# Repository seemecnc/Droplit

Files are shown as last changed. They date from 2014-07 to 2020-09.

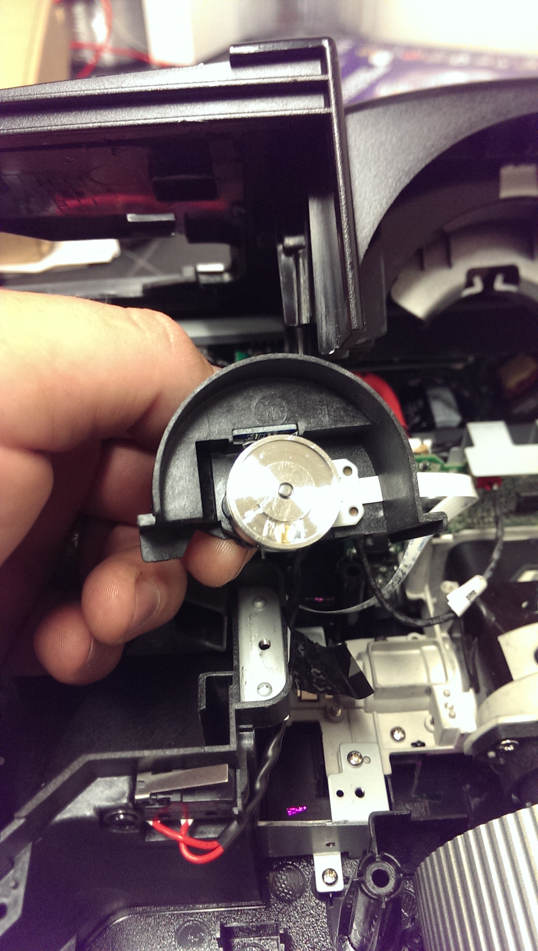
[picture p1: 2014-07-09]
DevPhotos/IMAG0862.jpg

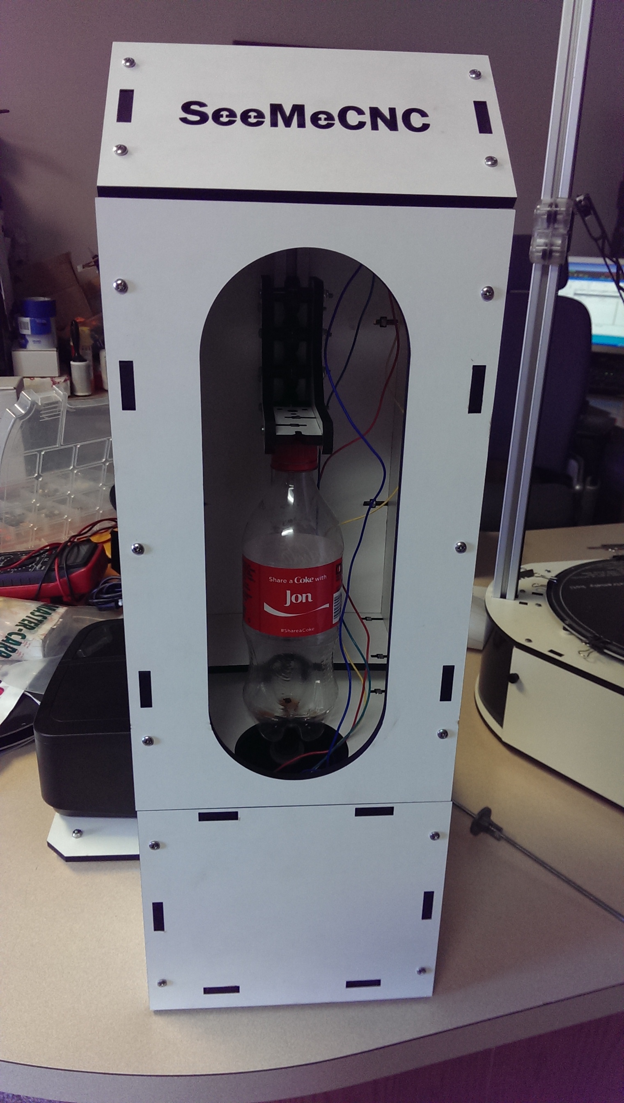
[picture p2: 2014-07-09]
DevPhotos/IMAG0863.jpg

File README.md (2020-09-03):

Droplit
=======

Droplit 3D Printer by SeeMeCNC

This project is released on good will by us.  All designs are originally drawn by us, however many of our ideas
may have obviously had influence from the RepRap community, hence the GPL license.  Feel free to use/modify these 
files for any reason, just share attribution if you do, thanks!

For the STL files, see http://repables.com/r/371/

Electronics/Firmware Used as of 7/14 are:

Arduino UNO r3 
http://arduino.cc

Grbl Shield by Synthetos
http://synthetos.com

Projector
TBD
Testing with IN Focus 116a and Acer P1283

Firmware is modified grbl 0.8c available from
http://github.com/grbl/grbl

# visit SeeMeCNC .com menu item SUPPORT for more docs & guides for RAMBo controlled SeeMeCNC 3D printers.

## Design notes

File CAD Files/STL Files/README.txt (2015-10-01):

38710 M5 Anti Backlash nut is used with M5x0.8 threaded rod and two TALL M5 nuts
One is sunk in the bottom of the part, then a spring (TBD) is put over the rod and
a second nut is then threaded on, and the spring takes out any backlash

You can just print Droplit_Plate.STL for all the required parts.

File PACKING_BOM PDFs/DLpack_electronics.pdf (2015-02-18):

# Packing List

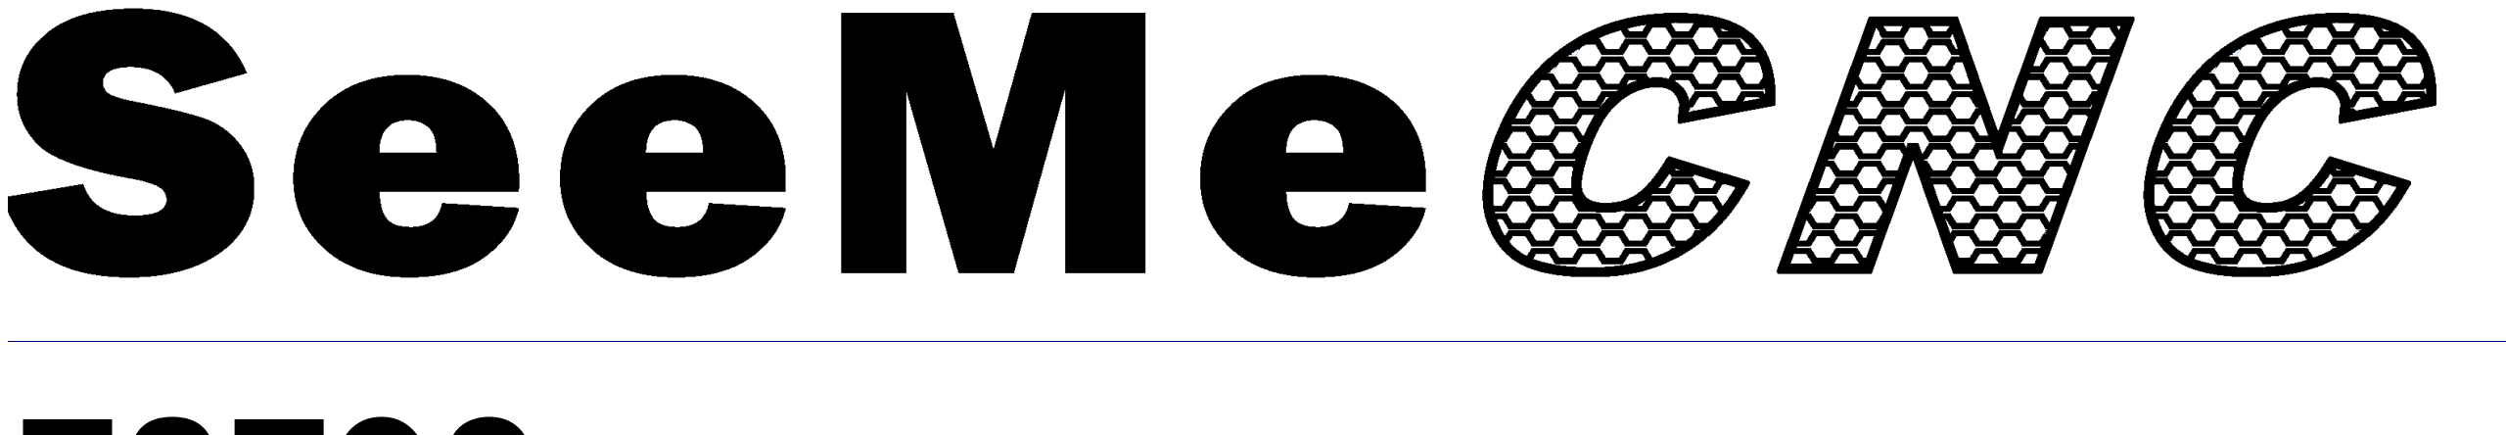
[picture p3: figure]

# 78793 DropLit Electronics Pack

item # | qty | Description | Where is this item used?
26801 | 1 | Arduino UNO R3 SMT | Electronics Bay
26802 | 1 | GShield 3 Axis Stepper Motor Board | Electronics Bay
26076 | 1 | SW143-ND SPDT Micro Switch | Top of TSLOT
26174 | 2 | Spade Terminal Crimp for Switch | Switch
26501 | 1 | Nema 17 Stepper Motor 4800gcm holding torque | Top of Machine
26175 | 1 | Rocker Switch, Black Round | Electronics Bay
26732 | 1 | ATX Power Supply 550 Watt Viotek | Electronics Bay
26164 | 8 | Wire Tie (small) | Frame
26728 | 3 | 26AWG 7 Strand Wire BLACK Thin Wall PVC | Electronics to End Stop (measured in feet)
26725 | 3 | 26AWG 7 Strand Wire WHITE Thin Wall PVC | Electronics to End Stop (measured in feet)
©2014 SeeMeCNC | 18-Feb-15 | 78793 | DropLit Electronics Pack | Page 1 of 1

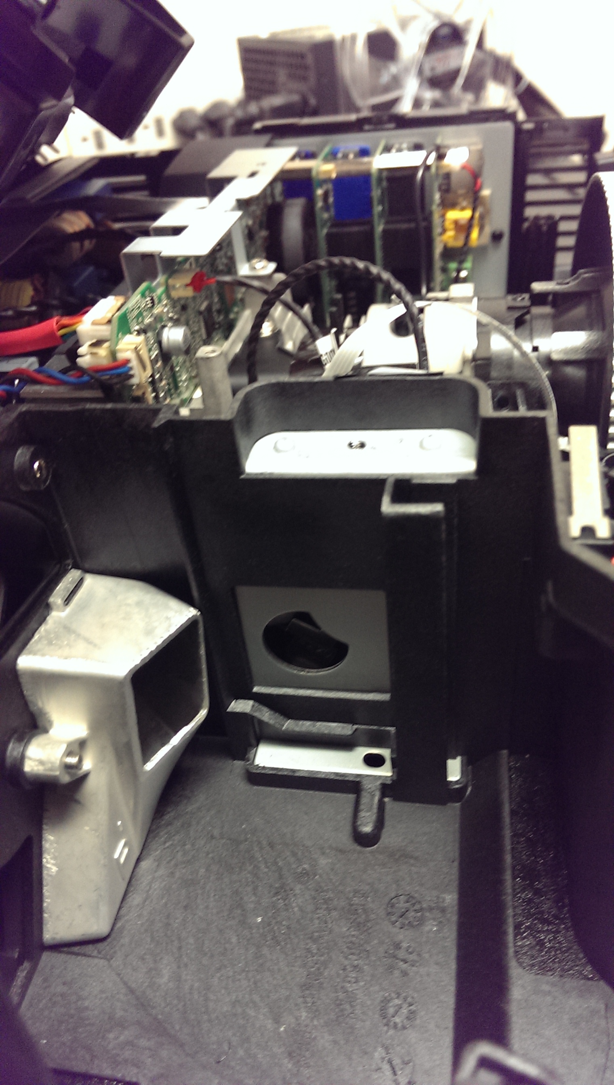
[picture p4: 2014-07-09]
DevPhotos/IMAG0861.jpg

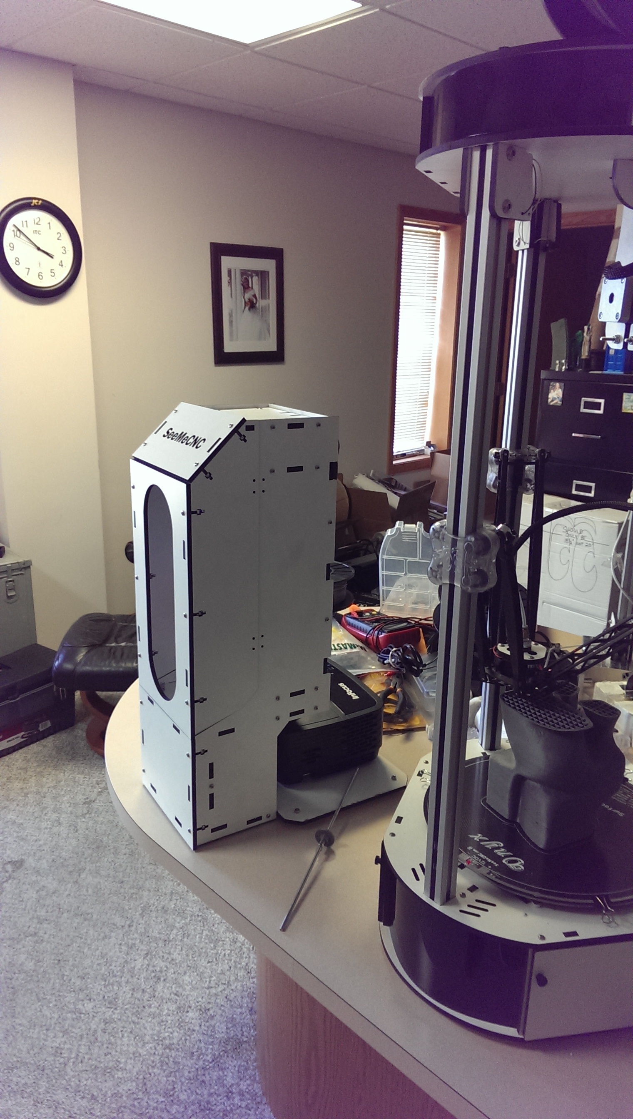
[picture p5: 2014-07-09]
DevPhotos/IMAG0865.jpg

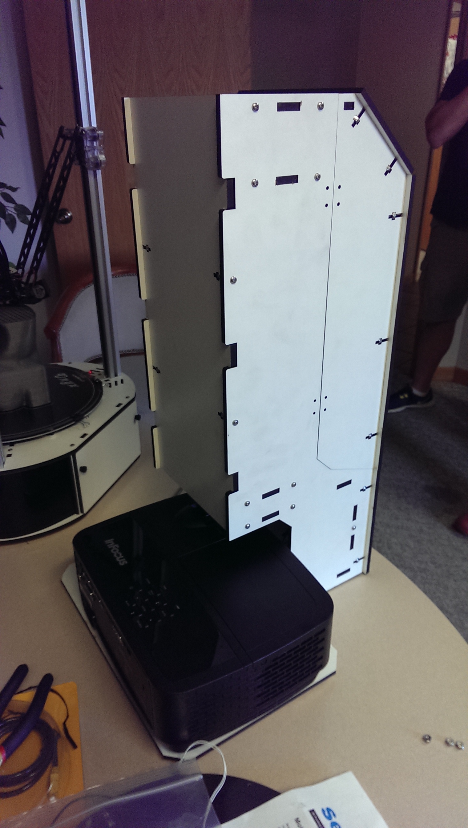
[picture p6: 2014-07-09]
DevPhotos/IMAG0864.jpg

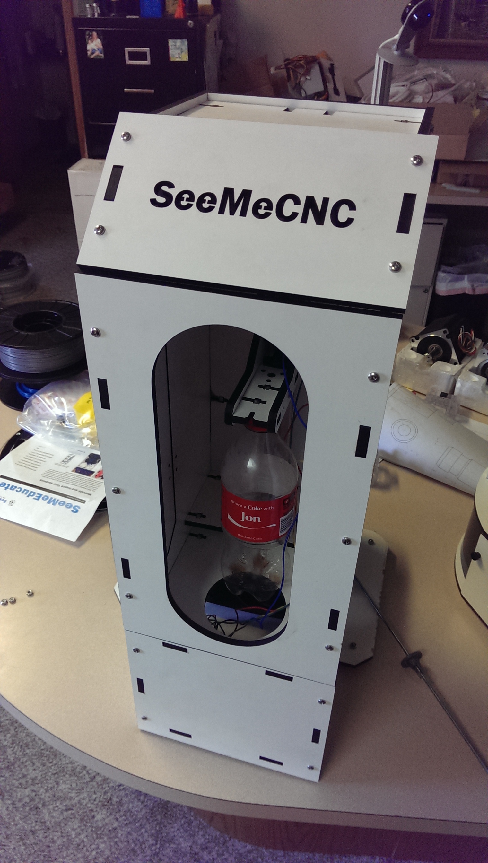
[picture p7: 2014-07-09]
DevPhotos/IMAG0866.jpg

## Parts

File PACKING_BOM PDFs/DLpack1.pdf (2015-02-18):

# Packing List

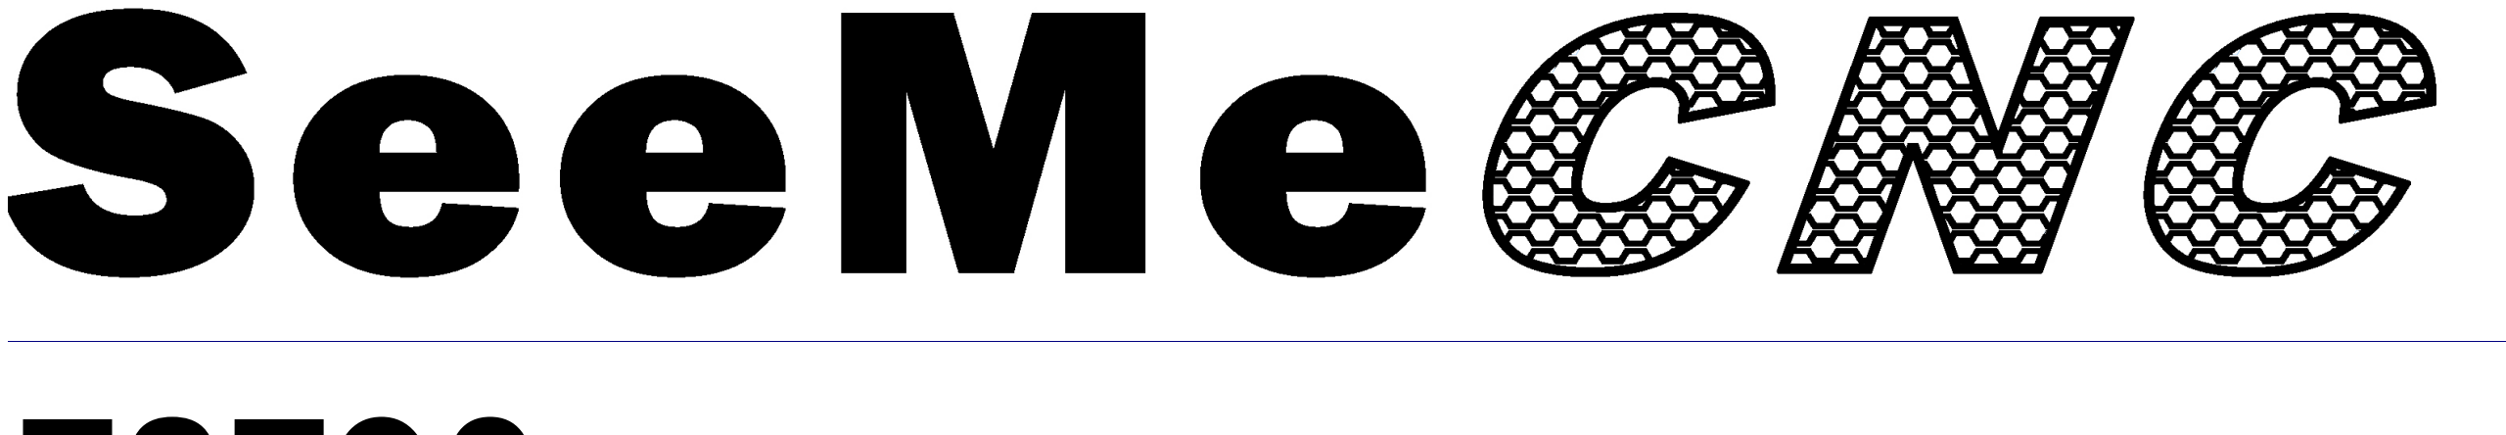
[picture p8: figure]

# 78790 DropLit Hardware Bag #1

item # | qty | Description | | Where is this item used?
30354 | 3 | M5 Zinc Plated Heavy Nut | Two used for anti backlash nut and one to secure z rod to coupler
35008 | 6 | 1/4ID x 5/8OD x .196W Ball Bearing R4ZZ | Cheapskate truck assembly
30033 | 57 | 6-32 x 1" L Phillip Pan Head Screw Stainless | Frame Assembly
30037 | 6 | 6-32 x 2.0" L Phillip Pan Head Screw 18-8 SS | Cheepskate Truck Assembly
30006 | 10 | SHCS 6-32 x 5/8" | 18-8 SS | Hinges and Door latch
30164 | 75 | 6-32 Nylon Lock Nut Stainless Steel | Entire Assembly
17505 | 4 | Leg for 44010 Foot | | Frame Base
44010 | 4 | Rubber Foot | | Frame Base
29998 | 4 | 10-32 x 5/8" Pan Head Screw Nylon | Frame Base
30170 | 4 | 10-32 Nylon Finish Nut | Frame Base
71505 | 4 | Plastic Bearing Roller 1/8"ID x 3/8"OD x 0.156"W | Electronics Mount
30121 | 4 | 6-32 x 1/2" Slotted Pan Head Screw Nylon | Power Supply
32005 | 6 | T SLOT Nut for 1" size 1/4-20 | TSLOT
30419 | 6 | 1/4-20 x 1/2" Button Head Cap Screw Stainless | TSLOT
30650 | 6 | 2-56 x 5/8"L Pan Head Phillips Machine Screw ( zinc plate ) | Attach Electronics
30642 | 6 | 2-56 Finish Nuts ( zine plate ) | Attach Electronics
30318 | 4 | M3 - .50 x1 0mm Phillip Pan Head Machine Screw 18-8 SS | Attach Stepper Motor
30449 | 4 | #4 SAE Flat Washer Stainless Steel | Attach Stepper Motor
30262 | 8 | #6 x 1/2"L Phillip Pan Head Sheet Metal Screw Type B Stainless | Vat Hold Down Assembly
31250 | 1 | .300 OD x .030 wire x 1/2L SS Compression spring | Antibacklash
30223 | 2 | 10-32 Blind T-Nut (Zinc Plate) | Vat Mount
30038 | 2 | M3-.5 x 6mm Set Screw Allen | Motor Coupler
30039 | 1 | 1.5mm Allen Key for M3-.5 set screws | Motor Coupler
30172 | 4 | 10-32 x 3/4" Knurled Thumb Screw Black Nylon | Mirror mount, vat hold down and platform
©2014 SeeMeCNC | 18-Feb-15 | 78790 | DropLit Hardware Bag #1 | Page 1 of 1

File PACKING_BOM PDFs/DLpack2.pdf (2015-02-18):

# Packing List

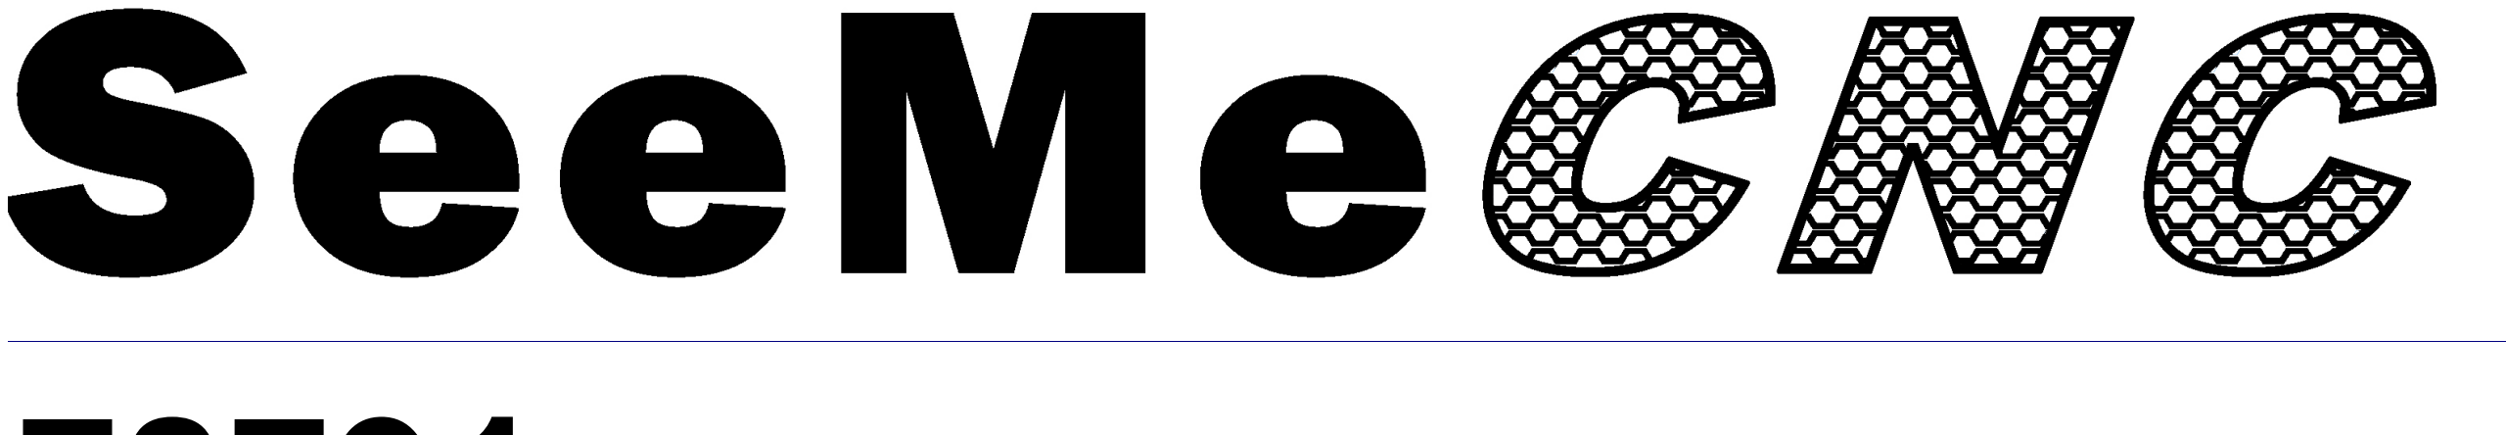
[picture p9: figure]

# 78791 DropLit Hardware Bag #2

item # | qty | Description | Where is this item used?
78704 | 6 | Eccentric Spacer | 0
38710 | 1 | M5 Anti Backlash Nut carrier | 0
78748 | 1 | Door Latch | 0
78755 | 2 | R4 Bearing Bushing Block | 0
78705 | 1 | M5 Threaded Rod 12" | Z Axis
38703 | 1 | 5mm Shaft Coupler | Z Axis
78702 | 1 | TSLOT - 15.25" | Z Axis
78749 | 1 | Build Plaform Standoff | Cheapskate Assembly
87941 | 12 | R4 Bearing Sleeve | Cheapskate Assembly
78740 | 2 | Hinge 1x1 | Door Hinges
78708 | 1 | Mirror 75mm x 75mm | Mirror
©2014 SeeMeCNC | 18-Feb-15 | 78791 | DropLit Hardware Bag #2 | Page 1 of 1

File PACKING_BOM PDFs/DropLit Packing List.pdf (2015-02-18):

# Packing List

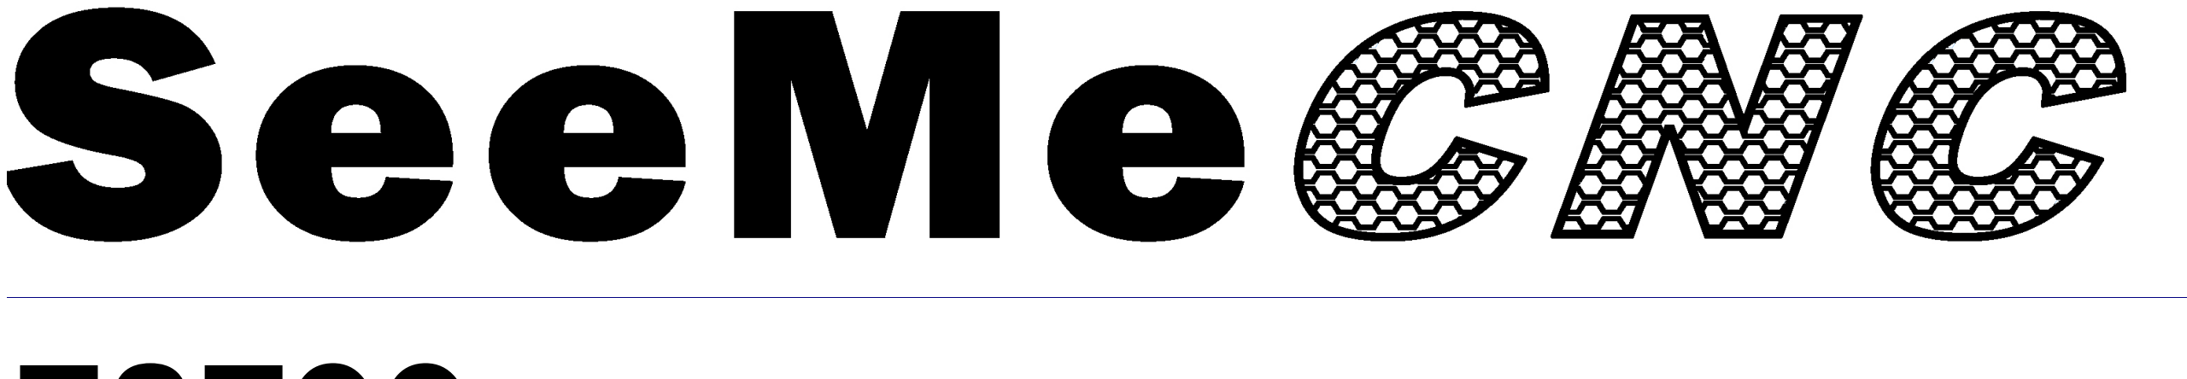
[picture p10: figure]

# 78799 DropLit DIY Kit

item # | qty | Description | Where is this item used?
78792 | 1 | DropLit Hardware Bag #3 | 0
78793 | 1 | DropLit Electronics Pack | 0
78791 | 1 | DropLit Hardware Bag #2 | 0
78790 | 1 | DropLit Hardware Bag #1 | 0
78794 | 1 | DropLit Lasercut Melamine Sheets (qty 4) | 0
78795 | 1 | DropLit Lasercut Acrylic Parts | 0
©2014 SeeMeCNC | 18-Feb-15 | 78799 | DropLit DIY Kit | Page 1 of 1

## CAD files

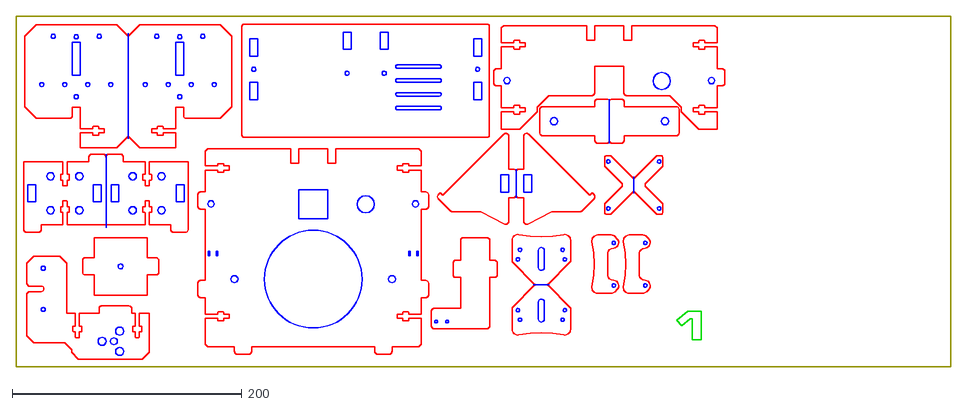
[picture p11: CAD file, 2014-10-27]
CAD Files/DXF LC Files/787xx Rev4/SHEET1.DXF
812.8 x 304.8

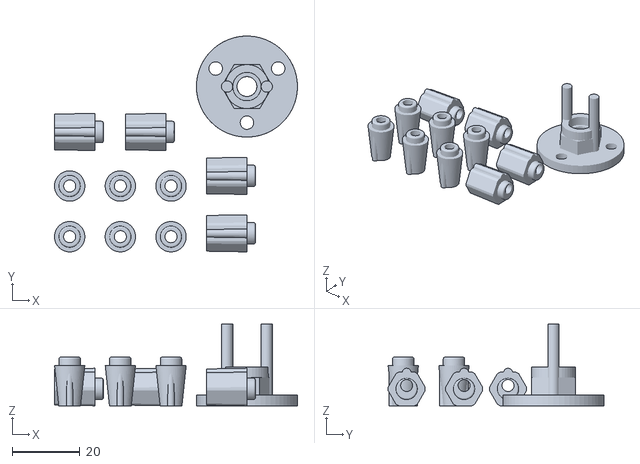
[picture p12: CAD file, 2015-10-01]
CAD Files/STL Files/Droplit_Plate.STL
71.9 x 63.9 x 24.1

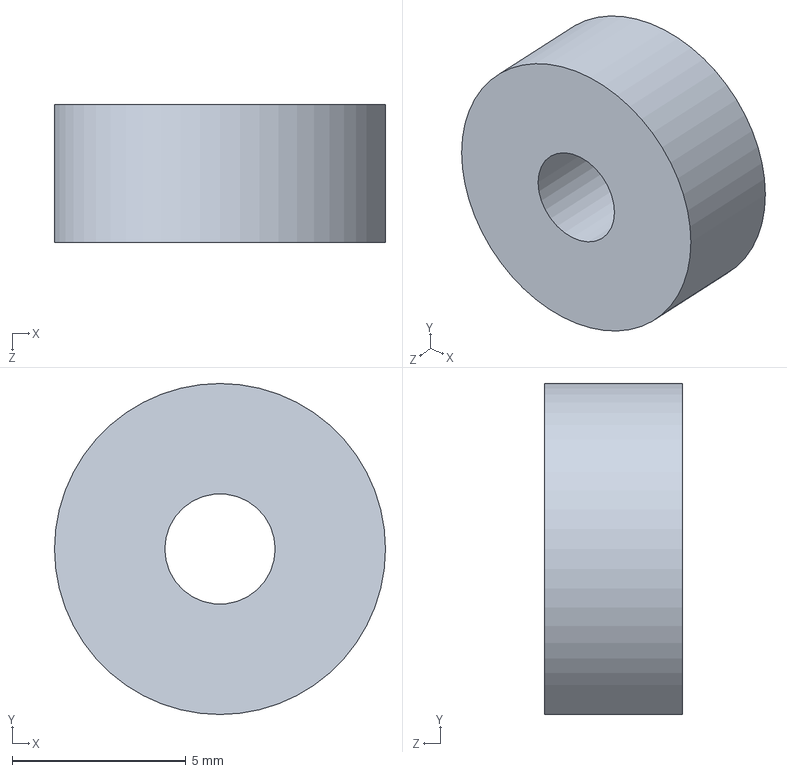
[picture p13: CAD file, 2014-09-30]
CAD Files/SW Files/plastic spacer.SLDPRT
9.53 x 9.53 x 3.96 mm

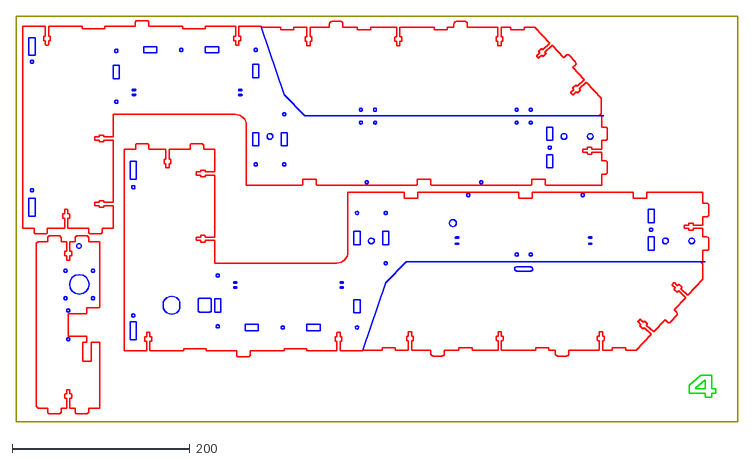
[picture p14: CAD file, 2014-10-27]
CAD Files/DXF LC Files/787xx Rev4/SHEET4.DXF
812.8 x 457.2

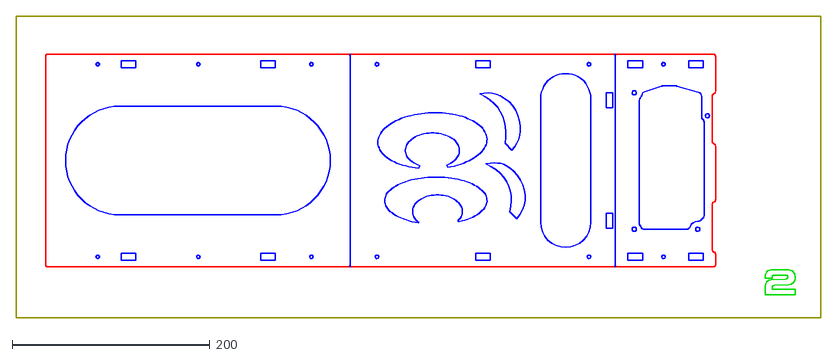
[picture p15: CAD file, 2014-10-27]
CAD Files/DXF LC Files/787xx Rev4/SHEET2.DXF
812.8 x 304.8

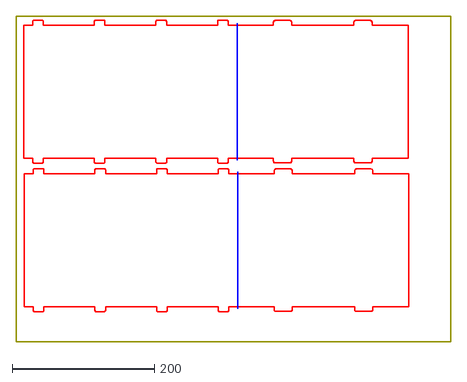
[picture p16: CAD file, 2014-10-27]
CAD Files/DXF LC Files/787xx Rev4/ACRYLICSHEET.DXF
609.6 x 457.2

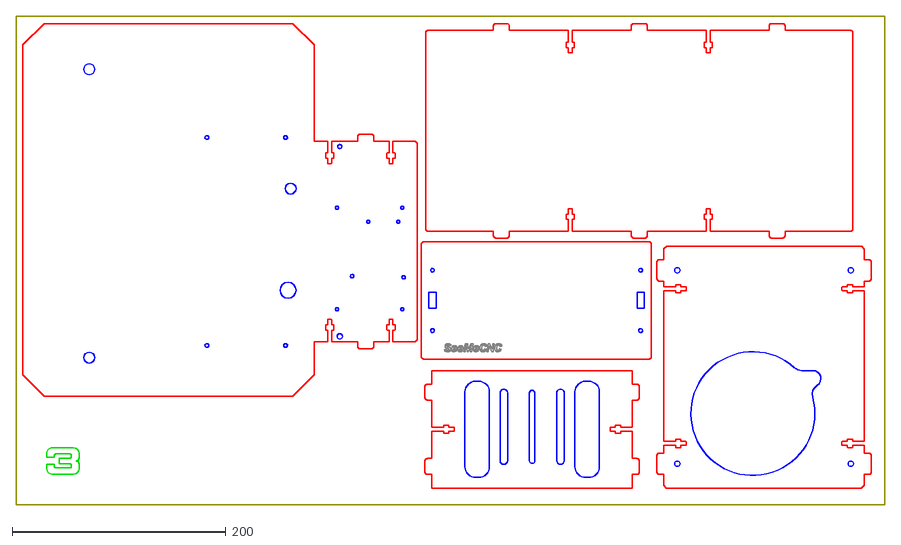
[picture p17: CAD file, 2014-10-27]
CAD Files/DXF LC Files/787xx Rev4/SHEET3.DXF
812.8 x 457.2

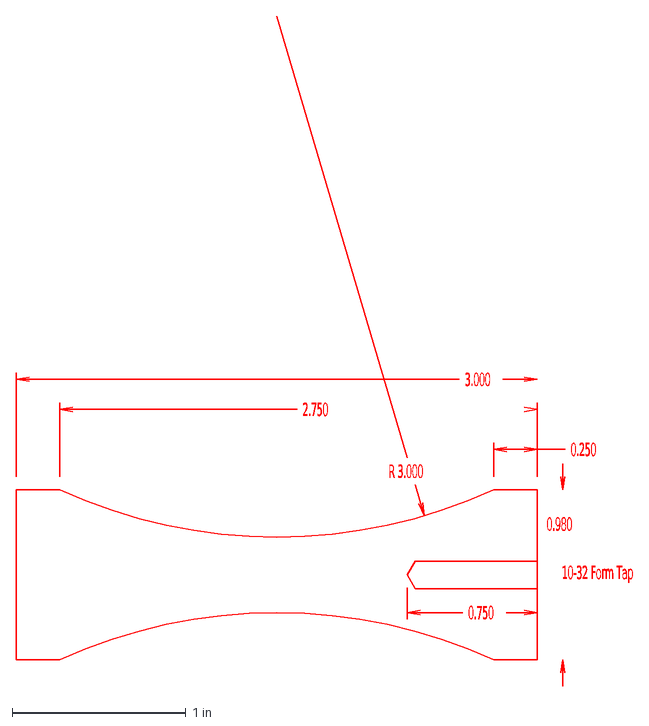
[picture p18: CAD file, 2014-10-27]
CAD Files/78749-PLATFORM-STANDOFF-ALUMINUM.DXF
10-32 Form Tap
0.980
0.250
3.000
0.750
2.750
R 3.000

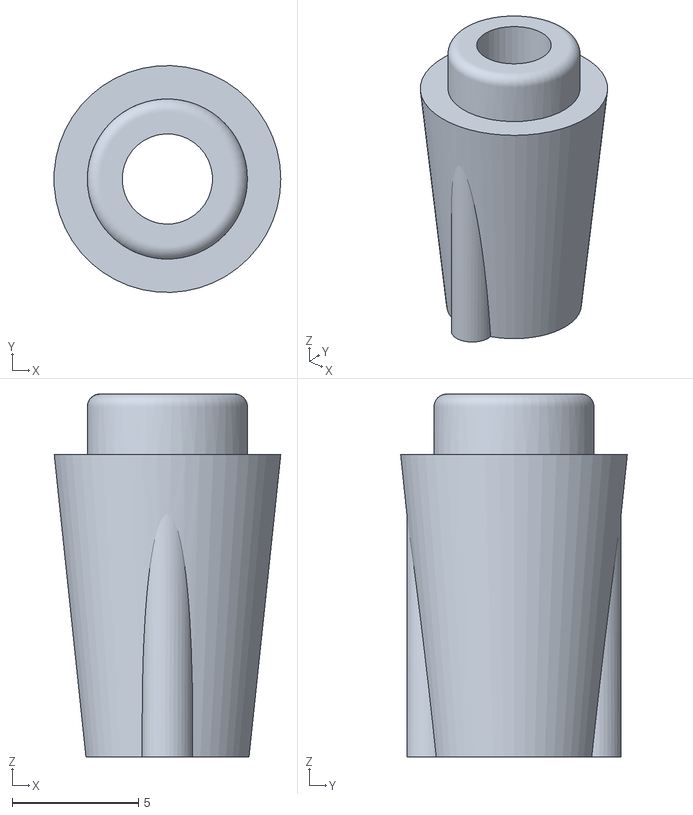
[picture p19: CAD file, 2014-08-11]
CAD Files/STL Files/78703 R4 Bearing Bushing.STL
8.99 x 9.00 x 14.4

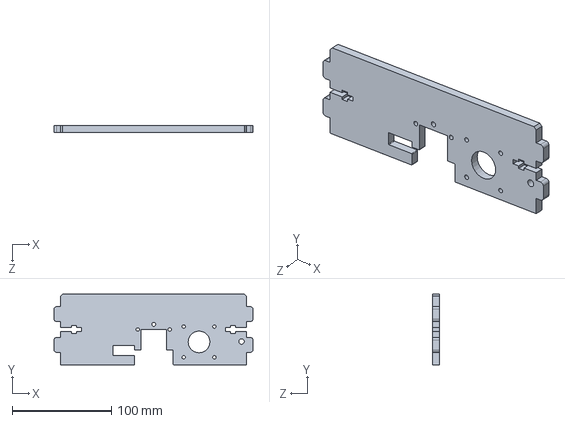
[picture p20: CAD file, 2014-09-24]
CAD Files/SW Files/78715 Motor Mount x1.SLDPRT
200.8 x 71.4 x 6.60 mm

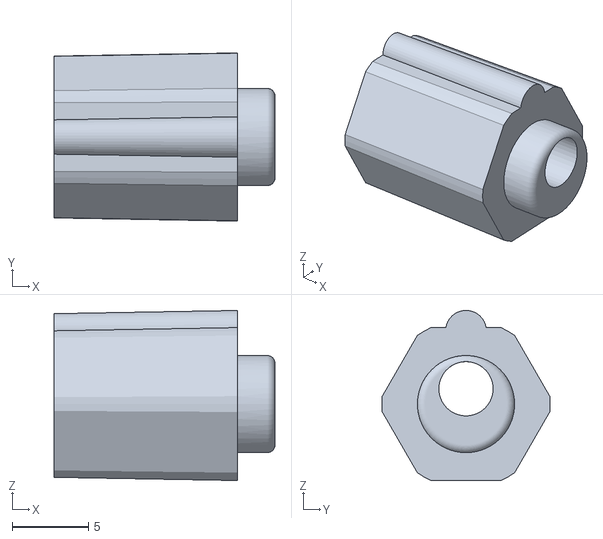
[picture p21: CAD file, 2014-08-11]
CAD Files/STL Files/78704 R4 Eccentric Bushing.STL
14.4 x 11.0 x 11.1

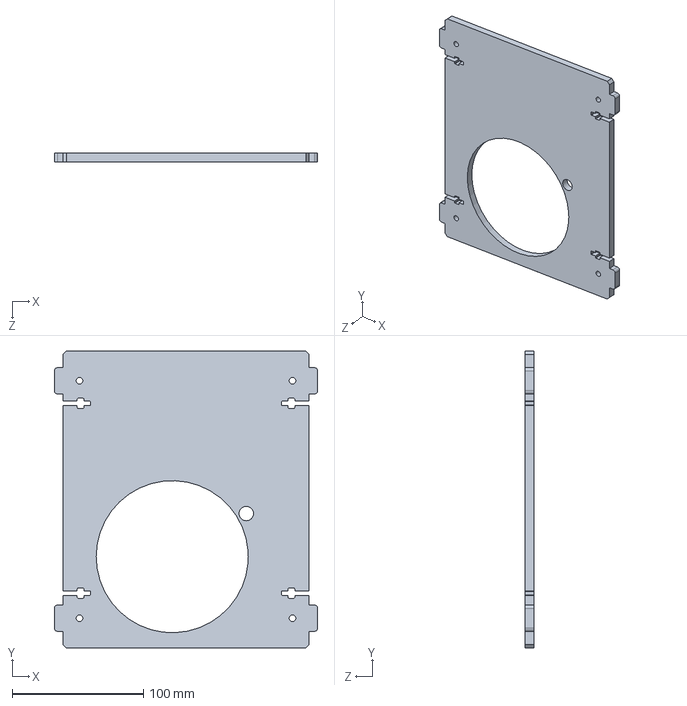
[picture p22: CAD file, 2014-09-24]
CAD Files/SW Files/78734 PSU Base Plate x1.SLDPRT
200.8 x 226.4 x 6.60 mm

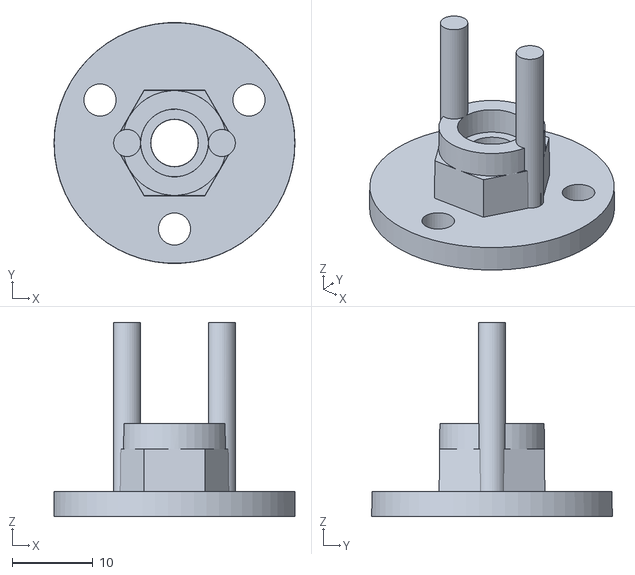
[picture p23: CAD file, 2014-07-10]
CAD Files/STL Files/38710 M5 Anti Backlash Nut Carrier.STL
29.9 x 29.9 x 24.1

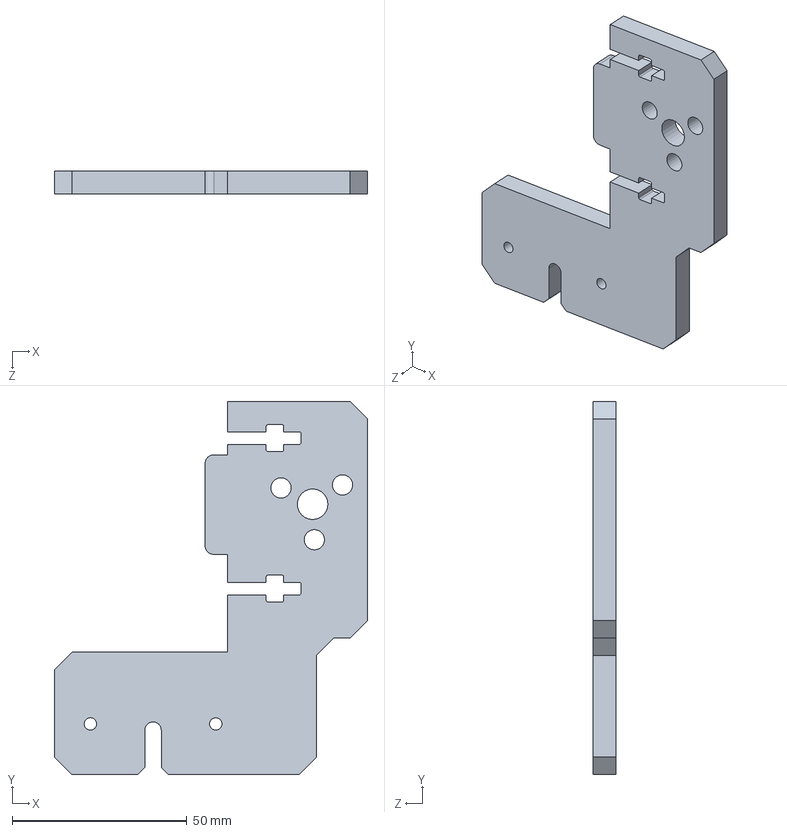
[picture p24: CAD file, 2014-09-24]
CAD Files/SW Files/78713 Carriage Mounting Plate for R4 x1.SLDPRT
89.6 x 106.7 x 6.60 mm

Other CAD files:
CAD Files/SW Files/78716 Top Plate x1.SLDPRT
CAD Files/DXF LC Files/787xx Rev4/78712 Base Side A x1.DXF
CAD Files/SW Files/78720 Back Cover x1.SLDPRT
CAD Files/DXF LC Files/787xx Rev4/78721 Cover Side A x1.DXF
CAD Files/DXF LC Files/787xx Rev1/ALLPARTS.DXF
CAD Files/DXF LC Files/787xx Rev2/78706 Window Panel x1 Acrylic.DXF
CAD Files/DXF LC Files/787xx Rev2/78710 DL Carriage Plate x2.DXF
CAD Files/DXF LC Files/787xx Rev2/78711 Base x1.DXF
CAD Files/DXF LC Files/787xx Rev2/78712 Base Side x2.DXF
CAD Files/DXF LC Files/787xx Rev2/78713 Carriage Mounting Plate for R4 x1.DXF
CAD Files/DXF LC Files/787xx Rev2/78714 Logo Panel x1 Acrylic.DXF
CAD Files/DXF LC Files/787xx Rev2/78715 Motor Mount x1.DXF
CAD Files/DXF LC Files/787xx Rev2/78716 Top Plate x1.DXF
CAD Files/DXF LC Files/787xx Rev2/78717 TSLOT Mount x2.DXF
CAD Files/DXF LC Files/787xx Rev2/78718 Dish Base x1..DXF
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

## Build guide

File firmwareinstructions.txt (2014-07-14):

Links for installing GRBL on an Arduino UNO

Download the hex file from this git repo
https://github.com/grbl/grbl-builds/blob/master/builds/grbl_v0_8c_atmega328p_16mhz_9600_build20131207.hex

Download XLoader from this link.  You will use it to upload the pre-compiled hex file downloaded above (the firmware)
http://russemotto.com/xloader

GRBL Wiki on GitHub describing how to compile it from source if you're super nerdy 
https://github.com/grbl/grbl/wiki/Compiling-Grbl

Instructions on using Grbl and how to modify it
https://github.com/grbl/grbl/wiki

To compile form source on windows download WinAVR
Install it in the DEFAULT DIRECTORY!!! which is usually C:...  DON'T CHANGE IT
in the default grbl folder, open a command prompt and run make clean then run make grbl.hex 
and you should be all good to go!

There is a file in the Firmware directory named configure.gcode that you can run to set the 
grbl defaults if you do not want to compile/etc... your own.  You can send that with any software to
the machine, or copy/past line be line the settings to configure the machine

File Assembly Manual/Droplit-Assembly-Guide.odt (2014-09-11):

Welcome to the Assembly Guide for the DropLit 3D printer.

Version 0.02, September 10th, 2014

Copyright 2014 by Gene Buckle

Licensed as Creative Commons Attribution-ShareAlike 3.0

Questions or corrections should be emailed to geneb@deltasoft.com

Disclaimer text provided by LulzBot

# READ ME FIRST!

READ THIS MANUAL COMPLETELY BEFORE ASSEMBLING AND POWERING UP

YOUR PRINTER!

###### Hazards and Warnings

###### The SeeMeCNC DropLit 3D printer has motorized parts. When the printer is in operation always be aware of possible hazards.

###### Electric Shock Hazard

###### Never open the electronics bay of the printer while the printer is powered on. Before removing

###### the access door, always power down the printer and unplug the AC line cord.

###### Fire Hazard

###### Never place flammable materials or liquids on or near the printer when powered on or in

###### operation.

###### Pinch Hazard

###### When the printer is in operation, take care to never put your fingers in the moving parts,

###### including the belts, pulleys or gears. Also, tie back long hair or clothing that can get caught in

###### the moving parts of the printer.

###### Static Charge

###### Make sure to ground yourself before touching the printer, especially the electronics.

###### Electrostatic charges can damage electronic components. To ground yourself, touch a

###### grounded source.

###### Age Warning

###### For users under the age of 18, adult supervision is recommended. Beware of choking hazards

###### around small children.

# 0 – Introduction and Acknowledgments

I’d like to welcome you to the DropLit assembly guide!

Please read this entire guide before you begin assembly of your new DropLit! It will help you avoid any unpleasant surprises and will ensure that you’ve got everything you need BEFORE you need it! Understand that the photographs in this assembly guide do NOT tell the whole story of each step! Make sure you read and understand the accompanying text for each step!

A quick note on the Arduino Uno and the “grbl” Shield. These two devices work in combination to control the DropLit and are very static sensitive, so please don't take them out of the bags they ship in until you're ready to install them.

# 1 – Required and Optional Tools And Materials

Before you begin assembly of your Rostock MAX v2, please make sure you’ve got everything on the following list of tools and additional materials.

- P1 & P2 sized Phillips screwdrivers
- Standard flat head screwdriver
- Wire strippers
- Wire cutters
- Battery powered screwdriver. If you ever needed an excuse to buy one of these, THIS IS IT.
- Blue thread locking compound (Loctite or Permatex Threadlocker Blue)
- Waxed lacing cord. You can use this in place of wire ties in pretty much any application. You can find it here: http://www.skygeek.com/wht-string.html. While expensive, you'll never really need to buy a wire tie again and it'll likely last you the rest of your life. :)

# 2 – Visual Bill of Materials

Your DropLit kit should contain a wrapped pack of Melamine parts, three bags of parts (two bags of hardware, one bag of electronic parts) a short section of aluminum extrusion and a power supply.

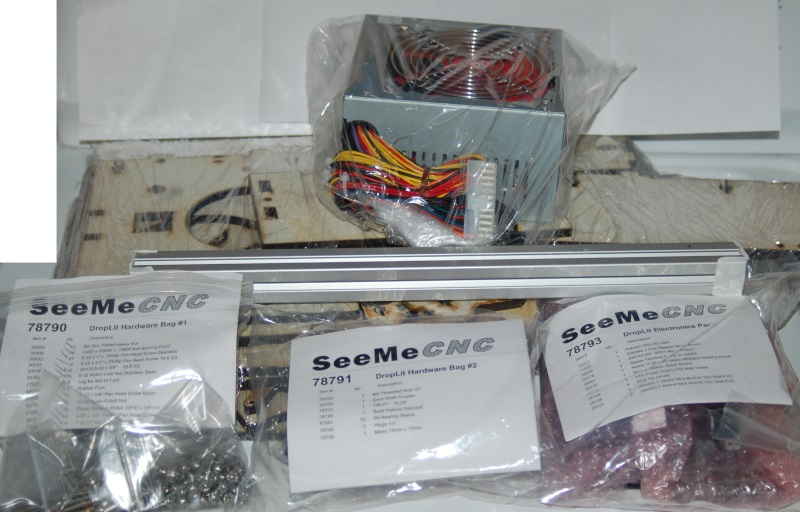
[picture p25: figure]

Fig. 2-1: DropLit package contents.

The Melamine parts are covered with a special cutting mask that prevents the laser cutting operation from depositing cutting residue on the Melamine surface. You'll need to remove all of this material before beginning construction. This process is called the Five Stages of Masking Tape.

1. Denial - Oh there's no way I need to scrape all this tape off those parts? Do I?

2. Anger - @#$%@#! This sucks! I've NEVER SEEN SO MUCH TAPE IN ONE PLACE IN MY LIFE!

3. Bargaining - “Well hi there, Significant Other! Would you PLEASE remove all this tape for me? PLEASE?”

4. Depression - This tape hates me. *sobs quietly*

5. Acceptance - Well I suppose if I'm ever going to get this thing built, I'd better get on with it and get all this tape removed...*sigh*

Ok, it's not THAT bad, it just seems like it. It beats having sticky ash product all over your nice and clean Melamine parts. :)

For those that aren't sure how to identify the various screw types, Bolt Depot has made available some excellent references. I would recommend Fastener Basics (http://www.boltdepot.com/fastener-information/Printable-Tools/Fastener-Basics.pdf) and their Fastener Type Chart (http://www.boltdepot.com/fastener-information/Type-Chart.aspx).

DropLit Hardware Bag #1

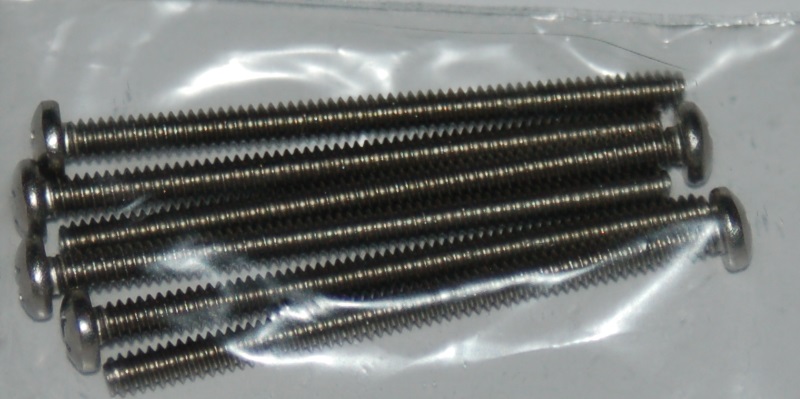
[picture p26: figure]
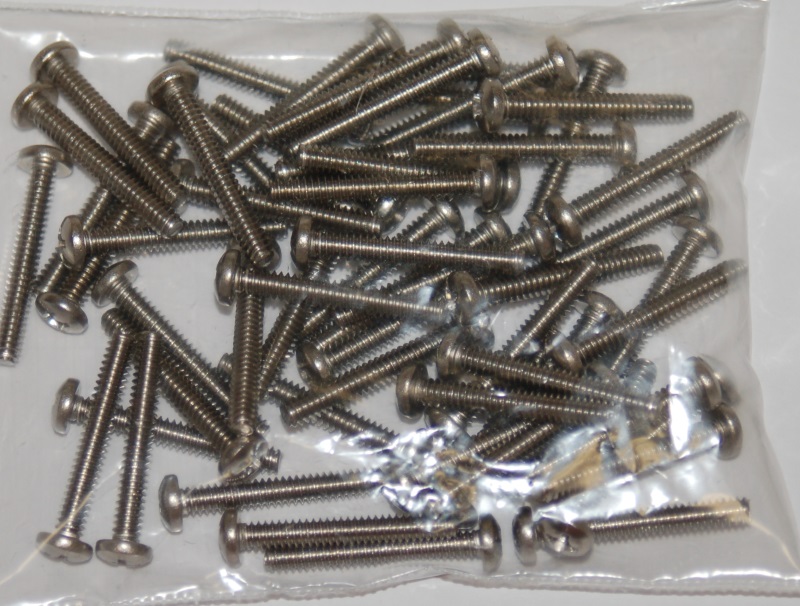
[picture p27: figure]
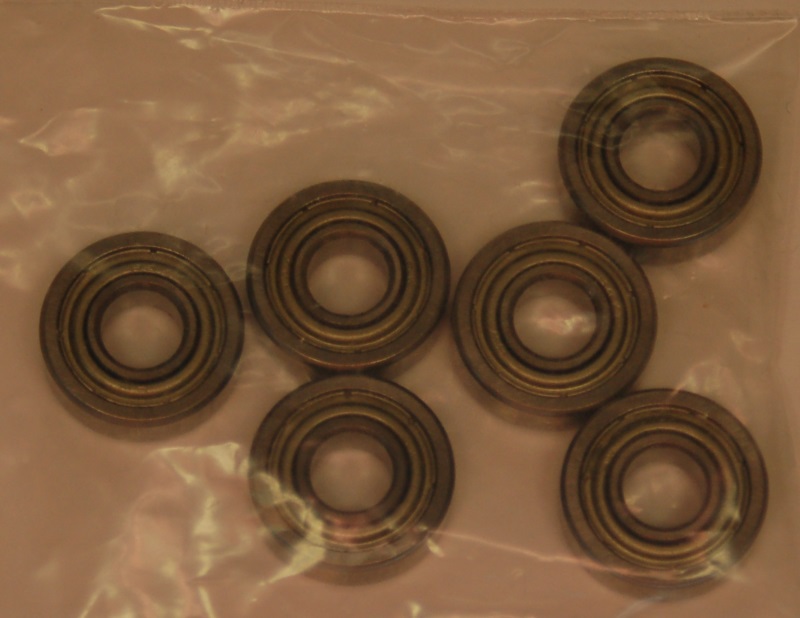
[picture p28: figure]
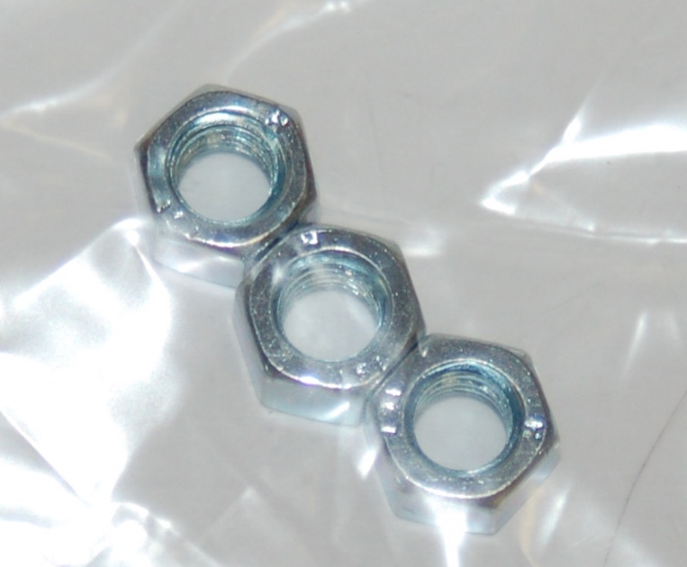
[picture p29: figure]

(___) (3) M5 Zinc Plated Nut

(___) (6) 1/4” ID x 5/8” OD x .196” Ball Bearing (R4ZZ)

(___) (57) #6-32 x 1” Phillips Pan Head Screw 18-8 SS

(___) (6) #6-32 x 2” Phillips Pan Head Screw 18-8 SS

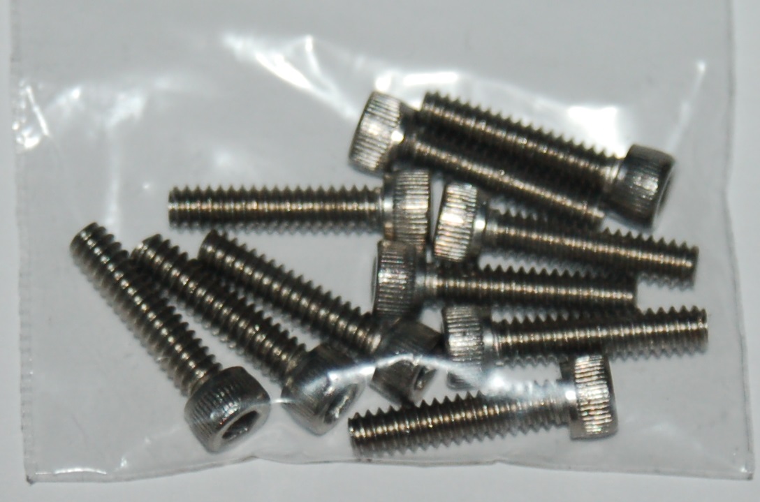
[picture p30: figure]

(___) (10) #6-32 x 5/8” Socket Head Cap Screw 18-8 SS

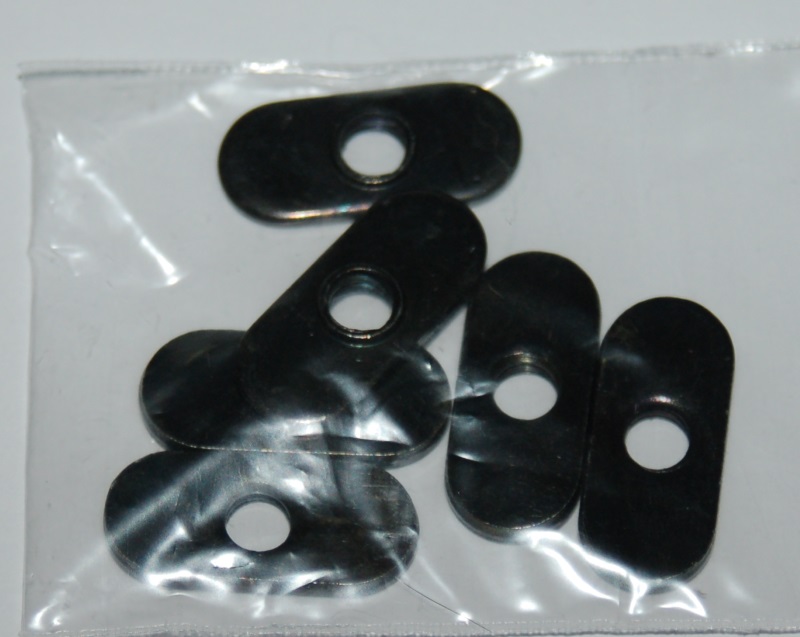
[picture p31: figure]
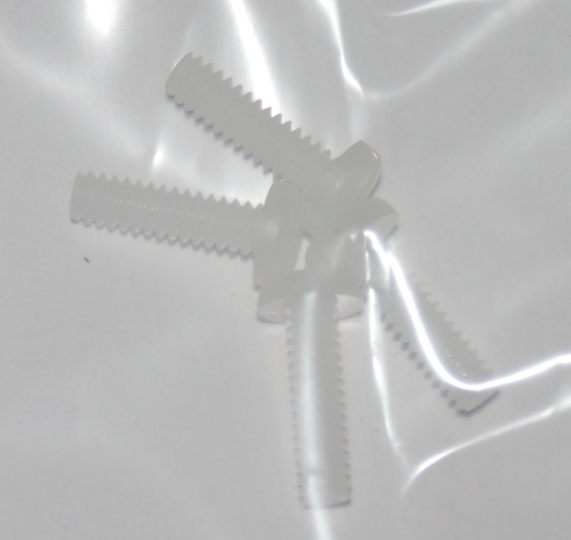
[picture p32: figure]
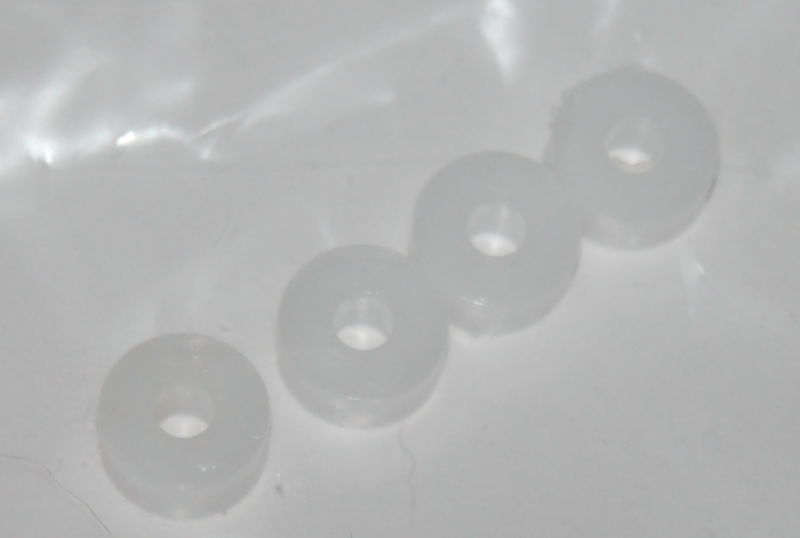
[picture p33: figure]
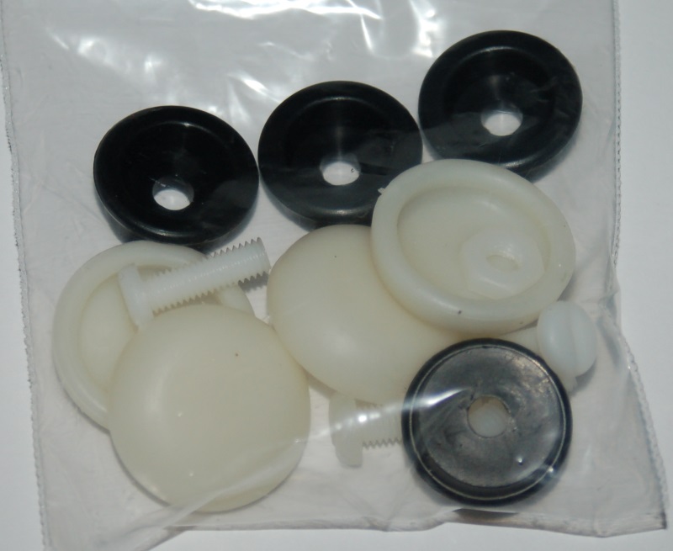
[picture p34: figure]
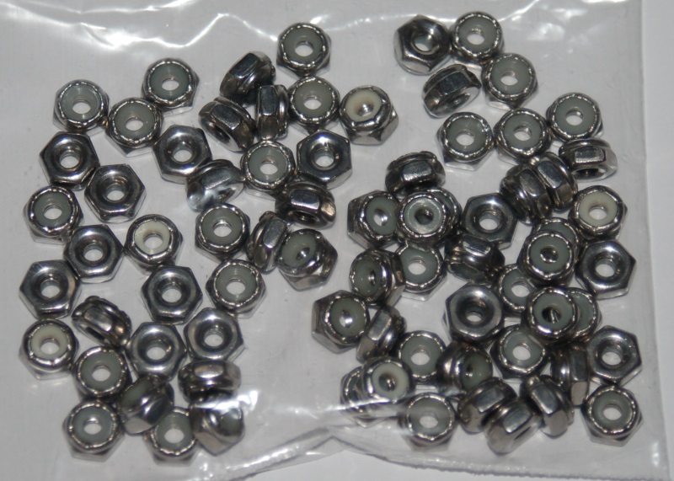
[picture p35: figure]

(___) (75) #6-32 Nylon Lock Nut SS

Rubber foot pack containing

(___) (4) Leg for 44010 Foot

(___) (4) Rubber Foot (44010)

(___) (4) #10-32 x 5/8” Pan Head Screw (Nylon)

(___) (4) #10-32 Nylon Finish Nut

(___) (4) Plastic Bearing Roller 1/8” ID x 3/8” OD x 0.156” W

(___) (4) #6-32 x 1/2” Slotted Pan Head Screw (Nylon)

(___) (6) 1/4-20 T-Slot Nut

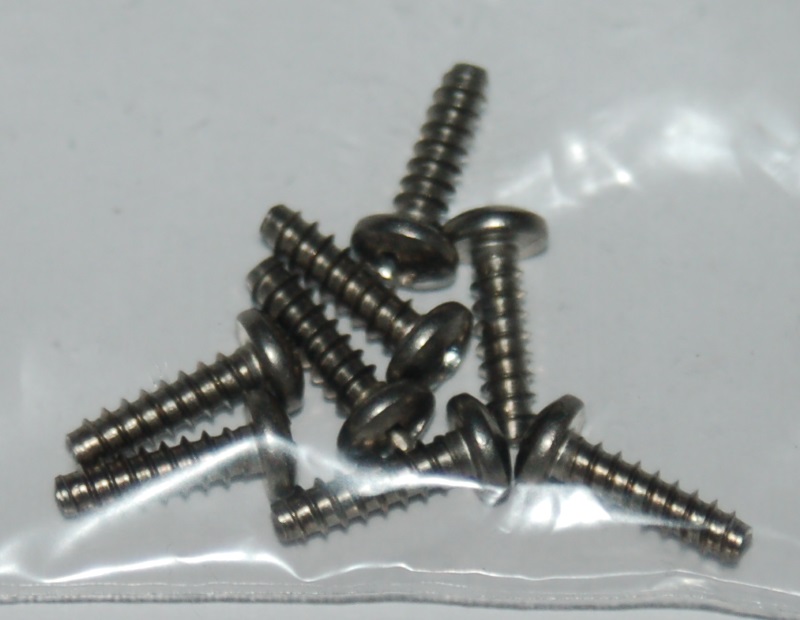
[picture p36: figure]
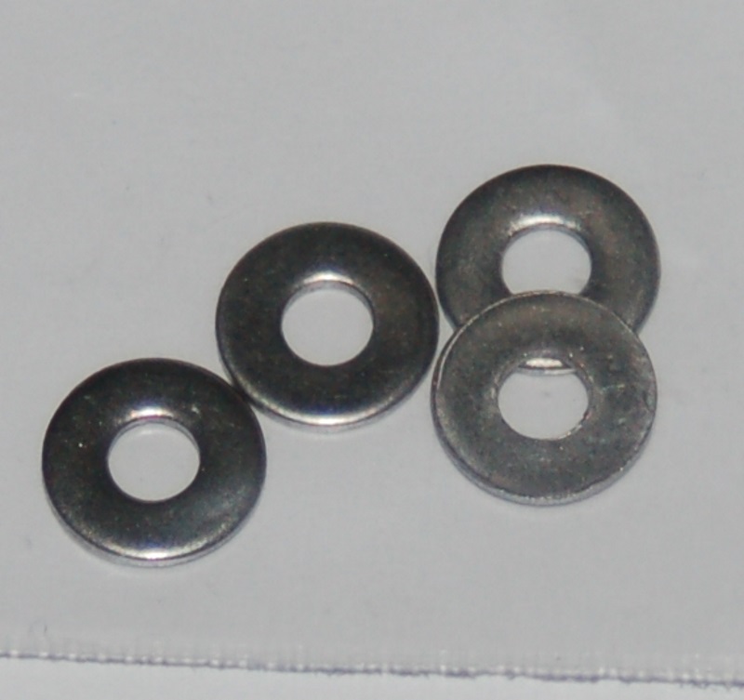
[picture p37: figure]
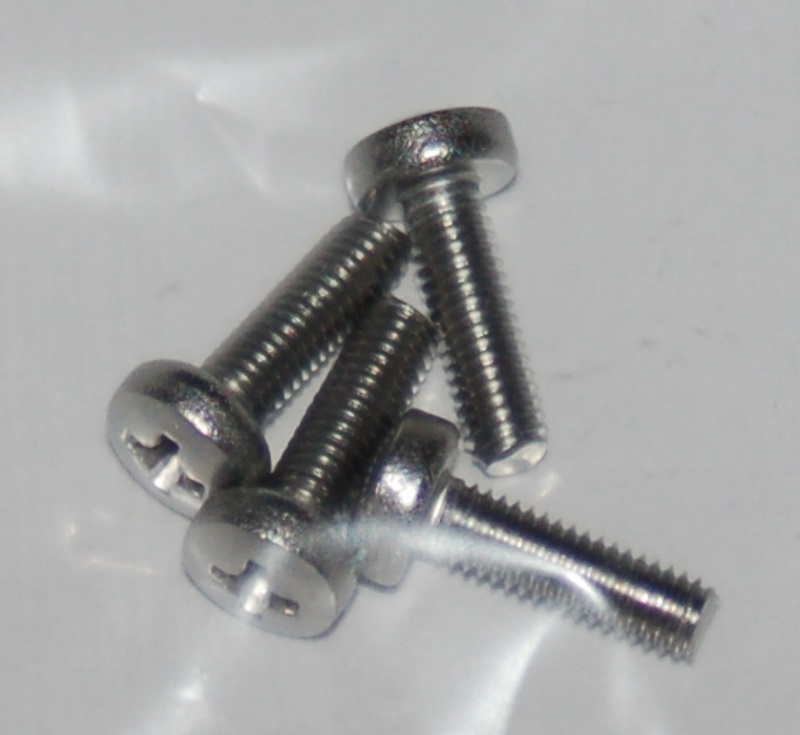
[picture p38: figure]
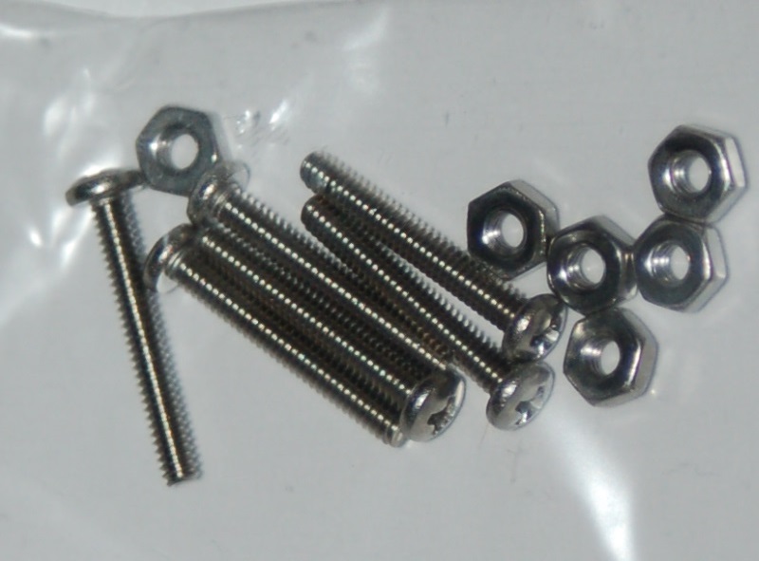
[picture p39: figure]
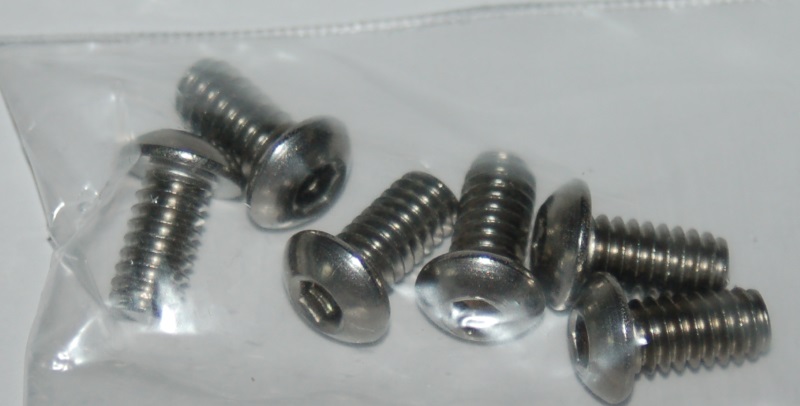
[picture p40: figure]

(___) (6) 1/4-20 x 1/2” Button Head Cap Screw (SS)

(___) (6) #2-56 x 5/8” Pan Head Screw

(___) (6) #2-56 Finish Nut

(___) (4) M3-.05 x 10mm Phillips Pan Head Screw (SS)

(___) (4) #4 SAE Flat Washer (SS)

(___) (8) #6 x 1/2” Phillips Pan Head Sheet Metal Screw (SS)

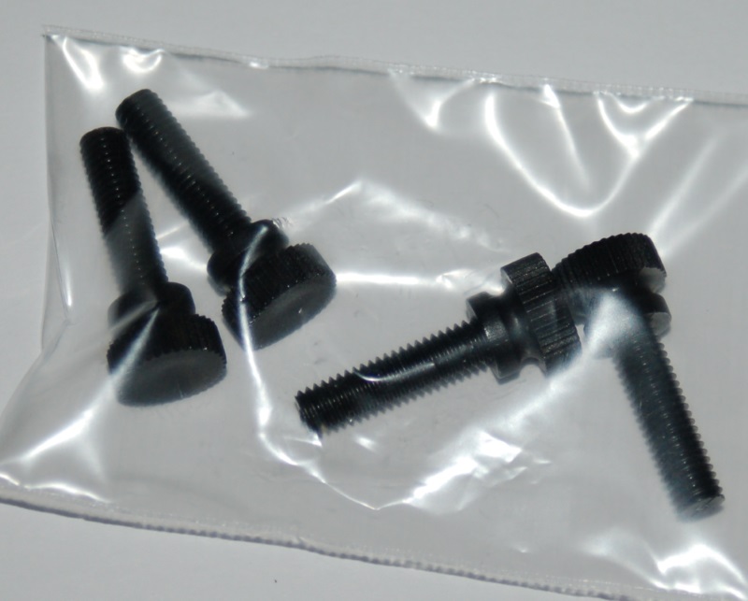
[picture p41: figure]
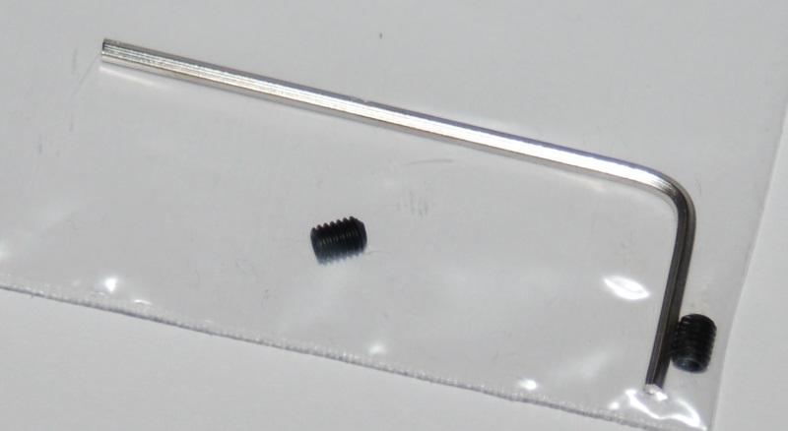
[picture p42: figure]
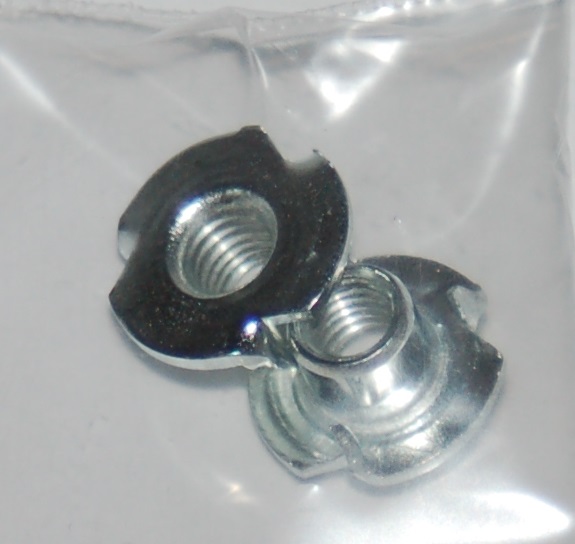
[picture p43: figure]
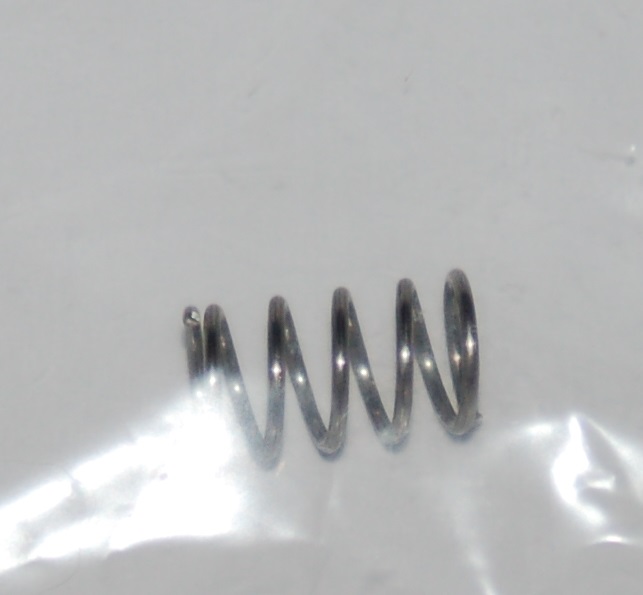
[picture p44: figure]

(___) (1) .300” OD x .030 wire x 1/2” SS Compression Spring

(___) (2) #10-32 T-Nut

(___) (2) M3-.5 x 6mm Allen Set Screw

(___) (1) 1.5mm Allen Wrench

(___) (4) #10-32 x 3/4” Knurled Thumb Screw (Black Nylon)

DropLit Assembly Guide

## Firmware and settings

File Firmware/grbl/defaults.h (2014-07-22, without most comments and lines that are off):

#define defaults_h
#ifdef DEFAULTS_GENERIC
  #define DEFAULT_X_STEPS_PER_MM 2000.0
  #define DEFAULT_Y_STEPS_PER_MM 2000.0
  #define DEFAULT_Z_STEPS_PER_MM 2000.0
  #define DEFAULT_STEP_PULSE_MICROSECONDS 44
  #define DEFAULT_MM_PER_ARC_SEGMENT 0.1
  #define DEFAULT_RAPID_FEEDRATE 300.0 // mm/min
  #define DEFAULT_FEEDRATE 300.0
  #define DEFAULT_ACCELERATION 25 // 10*60*60 mm/min^2 = 10 mm/s^2
  #define DEFAULT_JUNCTION_DEVIATION 0.05 // mm
  #define DEFAULT_STEPPING_INVERT_MASK ((1<<Y_DIRECTION_BIT)|(1<<Z_DIRECTION_BIT))
  #define DEFAULT_REPORT_INCHES 0 // false
  #define DEFAULT_AUTO_START 1 // true
  #define DEFAULT_INVERT_ST_ENABLE 0 // false
  #define DEFAULT_HARD_LIMIT_ENABLE 0  // false
  #define DEFAULT_HOMING_ENABLE 0  // false
  #define DEFAULT_HOMING_DIR_MASK 0 // move positive dir
  #define DEFAULT_HOMING_RAPID_FEEDRATE 200.0 // mm/min
  #define DEFAULT_HOMING_FEEDRATE 50.0 // mm/min
  #define DEFAULT_HOMING_DEBOUNCE_DELAY 100 // msec (0-65k)
  #define DEFAULT_HOMING_PULLOFF 3.0 // mm
  #define DEFAULT_STEPPER_IDLE_LOCK_TIME 200 // msec (0-255)
  #define DEFAULT_DECIMAL_PLACES 3
  #define DEFAULT_N_ARC_CORRECTION 25
#endif
#ifdef DEFAULTS_SEEMECNC_DL
  #define DEFAULT_X_STEPS_PER_MM 2000.0
  #define DEFAULT_Y_STEPS_PER_MM 2000.0
  #define DEFAULT_Z_STEPS_PER_MM 2000.0
  #define DEFAULT_STEP_PULSE_MICROSECONDS 44
  #define DEFAULT_MM_PER_ARC_SEGMENT 0.1
  #define DEFAULT_RAPID_FEEDRATE 300.0 // mm/min
  #define DEFAULT_FEEDRATE 300.0
  #define DEFAULT_ACCELERATION 15 // (10*60*60) mm/min^2 = 10 mm/s^2
  #define DEFAULT_JUNCTION_DEVIATION 0.05 // mm
  #define DEFAULT_STEPPING_INVERT_MASK 128
  #define DEFAULT_REPORT_INCHES 0 // false
  #define DEFAULT_AUTO_START 1 // true
  #define DEFAULT_INVERT_ST_ENABLE 0 // false
  #define DEFAULT_HARD_LIMIT_ENABLE 1  // false
  #define DEFAULT_HOMING_ENABLE 0  // false
  #define DEFAULT_HOMING_DIR_MASK 0 // move positive dir
  #define DEFAULT_HOMING_RAPID_FEEDRATE 250.0 // mm/min
  #define DEFAULT_HOMING_FEEDRATE 25.0 // mm/min
  #define DEFAULT_HOMING_DEBOUNCE_DELAY 100 // msec (0-65k)
  #define DEFAULT_HOMING_PULLOFF 0.5 // mm
  #define DEFAULT_STEPPER_IDLE_LOCK_TIME 200 // msec (0-255)
  #define DEFAULT_DECIMAL_PLACES 3
  #define DEFAULT_N_ARC_CORRECTION 25
#endif
#ifdef DEFAULTS_SHERLINE_5400
  #define MICROSTEPS 2
  #define STEPS_PER_REV 200.0
  #define MM_PER_REV (0.050*MM_PER_INCH) // 0.050 inch/rev leadscrew
  #define DEFAULT_X_STEPS_PER_MM (STEPS_PER_REV*MICROSTEPS/MM_PER_REV)
  #define DEFAULT_Y_STEPS_PER_MM (STEPS_PER_REV*MICROSTEPS/MM_PER_REV)
  #define DEFAULT_Z_STEPS_PER_MM (STEPS_PER_REV*MICROSTEPS/MM_PER_REV)
  #define DEFAULT_STEP_PULSE_MICROSECONDS 10
  #define DEFAULT_MM_PER_ARC_SEGMENT 0.1
  #define DEFAULT_RAPID_FEEDRATE 635.0 // mm/min (25ipm)
  #define DEFAULT_FEEDRATE 254.0 // mm/min (10ipm)
  #define DEFAULT_ACCELERATION 50.0*60*60 // 50*60*60 mm/min^2 = 50 mm/s^2
  #define DEFAULT_JUNCTION_DEVIATION 0.05 // mm
  #define DEFAULT_STEPPING_INVERT_MASK ((1<<Y_DIRECTION_BIT)|(1<<Z_DIRECTION_BIT))
  #define DEFAULT_REPORT_INCHES 1 // false
  #define DEFAULT_AUTO_START 1 // true
  #define DEFAULT_INVERT_ST_ENABLE 0 // false
  #define DEFAULT_HARD_LIMIT_ENABLE 0  // false
  #define DEFAULT_HOMING_ENABLE 0  // false
  #define DEFAULT_HOMING_DIR_MASK 0 // move positive dir
  #define DEFAULT_HOMING_RAPID_FEEDRATE 250.0 // mm/min
  #define DEFAULT_HOMING_FEEDRATE 25.0 // mm/min
  #define DEFAULT_HOMING_DEBOUNCE_DELAY 100 // msec (0-65k)
  #define DEFAULT_HOMING_PULLOFF 1.0 // mm
  #define DEFAULT_STEPPER_IDLE_LOCK_TIME 25 // msec (0-255)
  #define DEFAULT_DECIMAL_PLACES 3
  #define DEFAULT_N_ARC_CORRECTION 25
#endif
#ifdef DEFAULTS_SHAPEOKO
  #define MICROSTEPS_XY 8
  #define STEP_REVS_XY 400
  #define MM_PER_REV_XY (0.08*18*MM_PER_INCH) // 0.08 in belt pitch, 18 pulley teeth
  #define MICROSTEPS_Z 2
  #define STEP_REVS_Z 400
  #define MM_PER_REV_Z 1.250 // 1.25 mm/rev leadscrew
  #define DEFAULT_X_STEPS_PER_MM (MICROSTEPS_XY*STEP_REVS_XY/MM_PER_REV_XY)
  #define DEFAULT_Y_STEPS_PER_MM (MICROSTEPS_XY*STEP_REVS_XY/MM_PER_REV_XY)
  #define DEFAULT_Z_STEPS_PER_MM (MICROSTEPS_Z*STEP_REVS_Z/MM_PER_REV_Z)
  #define DEFAULT_STEP_PULSE_MICROSECONDS 10
  #define DEFAULT_MM_PER_ARC_SEGMENT 0.1
  #define DEFAULT_RAPID_FEEDRATE 1000.0 // mm/min
  #define DEFAULT_FEEDRATE 250.0
  #define DEFAULT_ACCELERATION (15.0*60*60) // 15*60*60 mm/min^2 = 15 mm/s^2
  #define DEFAULT_JUNCTION_DEVIATION 0.05 // mm
  #define DEFAULT_STEPPING_INVERT_MASK ((1<<Y_DIRECTION_BIT)|(1<<Z_DIRECTION_BIT))
  #define DEFAULT_REPORT_INCHES 0 // false
  #define DEFAULT_AUTO_START 1 // true
  #define DEFAULT_INVERT_ST_ENABLE 0 // false
  #define DEFAULT_HARD_LIMIT_ENABLE 0  // false
  #define DEFAULT_HOMING_ENABLE 0  // false
  #define DEFAULT_HOMING_DIR_MASK 0 // move positive dir
  #define DEFAULT_HOMING_RAPID_FEEDRATE 250.0 // mm/min
  #define DEFAULT_HOMING_FEEDRATE 25.0 // mm/min
  #define DEFAULT_HOMING_DEBOUNCE_DELAY 100 // msec (0-65k)
  #define DEFAULT_HOMING_PULLOFF 1.0 // mm
  #define DEFAULT_STEPPER_IDLE_LOCK_TIME 255 // msec (0-255)
  #define DEFAULT_DECIMAL_PLACES 3
  #define DEFAULT_N_ARC_CORRECTION 25
#endif
#ifdef DEFAULTS_SHAPEOKO_2
  #define MICROSTEPS_XY 8
  #define STEP_REVS_XY 200
  #define MM_PER_REV_XY (2*20) // 2mm belt pitch, 20 pulley teeth
  #define MICROSTEPS_Z 2
  #define STEP_REVS_Z 200
  #define MM_PER_REV_Z 1.250 // 1.25 mm/rev leadscrew
  #define DEFAULT_X_STEPS_PER_MM (MICROSTEPS_XY*STEP_REVS_XY/MM_PER_REV_XY)
  #define DEFAULT_Y_STEPS_PER_MM (MICROSTEPS_XY*STEP_REVS_XY/MM_PER_REV_XY)
  #define DEFAULT_Z_STEPS_PER_MM (MICROSTEPS_Z*STEP_REVS_Z/MM_PER_REV_Z)
  #define DEFAULT_STEP_PULSE_MICROSECONDS 30
  #define DEFAULT_MM_PER_ARC_SEGMENT 0.1
  #define DEFAULT_RAPID_FEEDRATE 500.0 // mm/min
  #define DEFAULT_FEEDRATE 500.0
  #define DEFAULT_ACCELERATION (25.0*60*60) // 25*60*60 mm/min^2 = 25 mm/s^2
  #define DEFAULT_JUNCTION_DEVIATION 0.05 // mm
  #define DEFAULT_STEPPING_INVERT_MASK ((1<<Y_DIRECTION_BIT)|(1<<Z_DIRECTION_BIT))
  #define DEFAULT_REPORT_INCHES 0 // false
  #define DEFAULT_AUTO_START 1 // true
  #define DEFAULT_INVERT_ST_ENABLE 0 // false
  #define DEFAULT_HARD_LIMIT_ENABLE 0  // false
  #define DEFAULT_HOMING_ENABLE 0  // false
  #define DEFAULT_HOMING_DIR_MASK 0 // move positive dir
  #define DEFAULT_HOMING_RAPID_FEEDRATE 250.0 // mm/min
  #define DEFAULT_HOMING_FEEDRATE 25.0 // mm/min
  #define DEFAULT_HOMING_DEBOUNCE_DELAY 100 // msec (0-65k)
  #define DEFAULT_HOMING_PULLOFF 1.0 // mm
  #define DEFAULT_STEPPER_IDLE_LOCK_TIME 255 // msec (0-255)
  #define DEFAULT_DECIMAL_PLACES 3
  #define DEFAULT_N_ARC_CORRECTION 25
#endif
#ifdef DEFAULTS_ZEN_TOOLWORKS_7x7
  #define MICROSTEPS 8
  #define STEPS_PER_REV 200.0
  #define MM_PER_REV 8.0 // 8 mm/rev leadscrew
  #define DEFAULT_X_STEPS_PER_MM (STEPS_PER_REV*MICROSTEPS/MM_PER_REV)
  #define DEFAULT_Y_STEPS_PER_MM (STEPS_PER_REV*MICROSTEPS/MM_PER_REV)
  #define DEFAULT_Z_STEPS_PER_MM (STEPS_PER_REV*MICROSTEPS/MM_PER_REV)
  #define DEFAULT_STEP_PULSE_MICROSECONDS 10
  #define DEFAULT_MM_PER_ARC_SEGMENT 0.1
  #define DEFAULT_RAPID_FEEDRATE 2500.0 // mm/min
  #define DEFAULT_FEEDRATE 1000.0 // mm/min
  #define DEFAULT_ACCELERATION 150.0*60*60 // 150*60*60 mm/min^2 = 150 mm/s^2
  #define DEFAULT_JUNCTION_DEVIATION 0.05 // mm
  #define DEFAULT_STEPPING_INVERT_MASK (1<<Y_DIRECTION_BIT)
  #define DEFAULT_REPORT_INCHES 0 // false
  #define DEFAULT_AUTO_START 1 // true
  #define DEFAULT_INVERT_ST_ENABLE 0 // false
  #define DEFAULT_HARD_LIMIT_ENABLE 0  // false
  #define DEFAULT_HOMING_ENABLE 0  // false
  #define DEFAULT_HOMING_DIR_MASK 0 // move positive dir
  #define DEFAULT_HOMING_RAPID_FEEDRATE 500.0 // mm/min
  #define DEFAULT_HOMING_FEEDRATE 50.0 // mm/min
  #define DEFAULT_HOMING_DEBOUNCE_DELAY 100 // msec (0-65k)
  #define DEFAULT_HOMING_PULLOFF 1.0 // mm
  #define DEFAULT_STEPPER_IDLE_LOCK_TIME 25 // msec (0-255)
  #define DEFAULT_DECIMAL_PLACES 3
  #define DEFAULT_N_ARC_CORRECTION 25
#endif

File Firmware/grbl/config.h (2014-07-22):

/*
  config.h - compile time configuration
  Part of Grbl

  The MIT License (MIT)

  GRBL(tm) - Embedded CNC g-code interpreter and motion-controller
  Copyright (c) 2009-2011 Simen Svale Skogsrud
  Copyright (c) 2011-2013 Sungeun K. Jeon

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
  THE SOFTWARE IS PROVIDED "AS IS", WITHOUT WARRANTY OF ANY KIND, EXPRESS OR
  IMPLIED, INCLUDING BUT NOT LIMITED TO THE WARRANTIES OF MERCHANTABILITY,
  FITNESS FOR A PARTICULAR PURPOSE AND NONINFRINGEMENT. IN NO EVENT SHALL THE
  AUTHORS OR COPYRIGHT HOLDERS BE LIABLE FOR ANY CLAIM, DAMAGES OR OTHER
  LIABILITY, WHETHER IN AN ACTION OF CONTRACT, TORT OR OTHERWISE, ARISING FROM,
  OUT OF OR IN CONNECTION WITH THE SOFTWARE OR THE USE OR OTHER DEALINGS IN
  THE SOFTWARE.
*/

// This file contains compile-time configurations for Grbl's internal system. For the most part,
// users will not need to directly modify these, but they are here for specific needs, i.e.
// performance tuning or adjusting to non-typical machines.

// IMPORTANT: Any changes here requires a full re-compiling of the source code to propagate them.

#ifndef config_h
#define config_h

// Default settings. Used when resetting EEPROM. Change to desired name in defaults.h
#define DEFAULTS_SEEMECNC_DL

// Serial baud rate
#define BAUD_RATE 9600

// Default pin mappings. Grbl officially supports the Arduino Uno only. Other processor types
// may exist from user-supplied templates or directly user-defined in pin_map.h
#define PIN_MAP_ARDUINO_UNO

// Define runtime command special characters. These characters are 'picked-off' directly from the
// serial read data stream and are not passed to the grbl line execution parser. Select characters
// that do not and must not exist in the streamed g-code program. ASCII control characters may be 
// used, if they are available per user setup. Also, extended ASCII codes (>127), which are never in 
// g-code programs, maybe selected for interface programs.
// NOTE: If changed, manually update help message in report.c.
#define CMD_STATUS_REPORT '?'
#define CMD_FEED_HOLD '!'
#define CMD_CYCLE_START '~'
#define CMD_RESET '%' // changed from ctrl-x to %  j.o.

// The temporal resolution of the acceleration management subsystem. Higher number give smoother
// acceleration but may impact performance.
// NOTE: Increasing this parameter will help any resolution related issues, especially with machines 
// requiring very high accelerations and/or very fast feedrates. In general, this will reduce the 
// error between how the planner plans the motions and how the stepper program actually performs them.
// However, at some point, the resolution can be high enough, where the errors related to numerical 
// round-off can be great enough to cause problems and/or it's too fast for the Arduino. The correct
// value for this parameter is machine dependent, so it's advised to set this only as high as needed.
// Approximate successful values can range from 30L to 100L or more.
#define ACCELERATION_TICKS_PER_SECOND 50L

// Minimum planner junction speed. Sets the default minimum speed the planner plans for at the end
// of the buffer and all stops. This should not be much greater than zero and should only be changed
// if unwanted behavior is observed on a user's machine when running at very slow speeds.
#define MINIMUM_PLANNER_SPEED 0.0 // (mm/min)

// Minimum stepper rate. Sets the absolute minimum stepper rate in the stepper program and never runs
// slower than this value, except when sleeping. This parameter overrides the minimum planner speed.
// This is primarily used to guarantee that the end of a movement is always reached and not stop to
// never reach its target. This parameter should always be greater than zero.
#define MINIMUM_STEPS_PER_MINUTE 800 // (steps/min) - Integer value only

// Time delay increments performed during a dwell. The default value is set at 50ms, which provides
// a maximum time delay of roughly 55 minutes, more than enough for most any application. Increasing
// this delay will increase the maximum dwell time linearly, but also reduces the responsiveness of 
// run-time command executions, like status reports, since these are performed between each dwell 
// time step. Also, keep in mind that the Arduino delay timer is not very accurate for long delays.
#define DWELL_TIME_STEP 50 // Integer (1-255) (milliseconds)

// If homing is enabled, homing init lock sets Grbl into an alarm state upon power up. This forces
// the user to perform the homing cycle (or override the locks) before doing anything else. This is
// mainly a safety feature to remind the user to home, since position is unknown to Grbl.
//#define HOMING_INIT_LOCK // Comment to disable
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

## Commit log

2014-07-09 Adding experimental firmware folders
    Adding a GRBL and Sprinter Firmware folder
    [Configuration.h, config.h, defaults.h]
2014-07-09 Adding firmware instructions etc...
    Added some instructions on how to get/install Grbl on an Uno a nd other
    misc. edits
    [Configuration.h, config.h, defaults.h]
2014-07-09 Added First draft LC files
    Added first LC files etc...
    [ALLPARTS.DXF]
2014-07-10 Added STL file for prototype backlash nut
    added anti backlash nut stl
    [38710 M5 Anti Backlash Nut Carrier.STL]
2014-07-14 Updated firmware files
    Updating firmware setups
    [config.h, defaults.h]
2014-07-21 Rev2 CAD files released
    Updated to Rev 2 CAD dxf files
    [78706 Window Panel x1 Acrylic.DXF, 78710 DL Carriage Plate x2.DXF, 78711 Base x1.DXF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]
2014-07-22 updated firmware
    Modified firmware verbage and defaults
    [config.h, defaults.h]
2014-07-22 edited grbl stuffs
    edited grbl configs and added home/limit switch to machine to prevent
    machine self destruct sequence :)
    [config.h, defaults.h]
2014-08-11 Updated DXF and STL folders
    Updated files to Rev3 versions
    [78703 R4 Bearing Bushing.STL, 78704 R4 Eccentric Bushing.STL, 78706 Window Panel x1Acrylic.DXF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]
2014-08-11 Rotated Bearing Bushing to make it printable
    [78703 R4 Bearing Bushing.STL]
2014-08-11 Added a plate for easy printing
    [Droplit_Plate.STL]
2014-08-15 Updated all CAD files
    Updated DXF's for droplit, added new holes for mini-Rambo mounting for
    future use, corrected some misaligned LC holes etc...
    [78706 Window Panel x1Acrylic.DXF, 78711 Base x1.DXF, 78712 Base Side x2.DXF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]
2014-09-24 Added full bill of materials
    [78706 Window Panel x1Acrylic.SLDPRT, 78710 DL Carriage Plate x2.SLDPRT, 78711 Base x1.SLDPRT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]
2014-09-30 Assembly portion of the build manual is completed!
    [plastic spacer.SLDPRT]
2014-10-17 updated DXF files to rev4
    rev4 files added
    [78706 Window Panel ACRYLIC x1.DXF, 78710 DL Carriage Plate x2.DXF, 78711 Base x1.DXF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]
2014-10-27 Added platform DXF file
    Added DXF file for machined aluminum build platform
    [78749-PLATFORM-STANDOFF-ALUMINUM.DXF]
2014-10-27 Updated DXF's
    Updated DXF's and added LC acrylic sheets
    [ACRYLICSHEET.DXF, SHEET1.DXF, SHEET2.DXF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]
2015-02-18 Added Packing and BOM folder
    Added internal packing lists and BOM's

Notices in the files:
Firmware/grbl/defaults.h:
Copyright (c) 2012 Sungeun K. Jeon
